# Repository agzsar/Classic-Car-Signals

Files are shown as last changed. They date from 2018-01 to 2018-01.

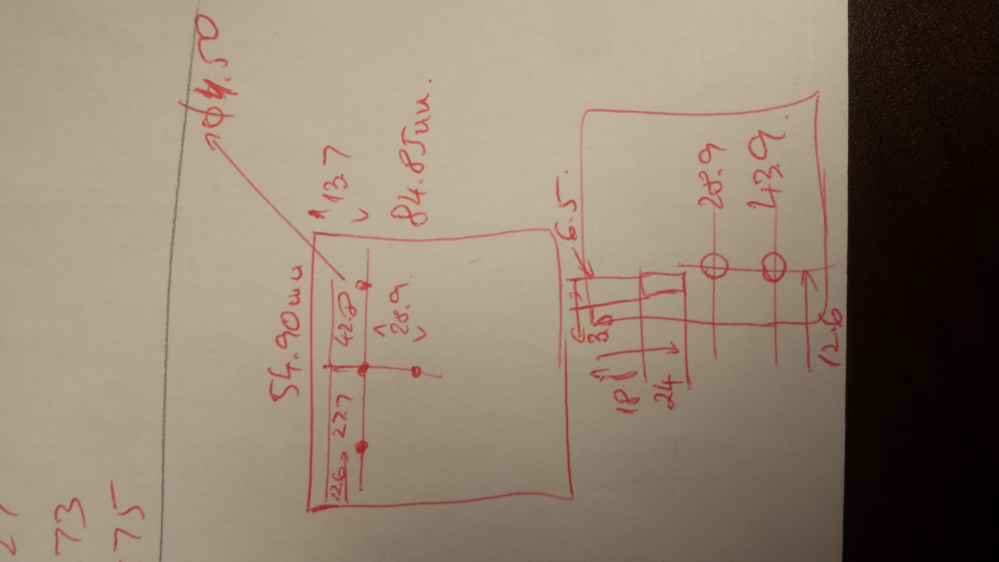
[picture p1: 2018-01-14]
9_Drawings/Remote Labels/Measurements.jpg

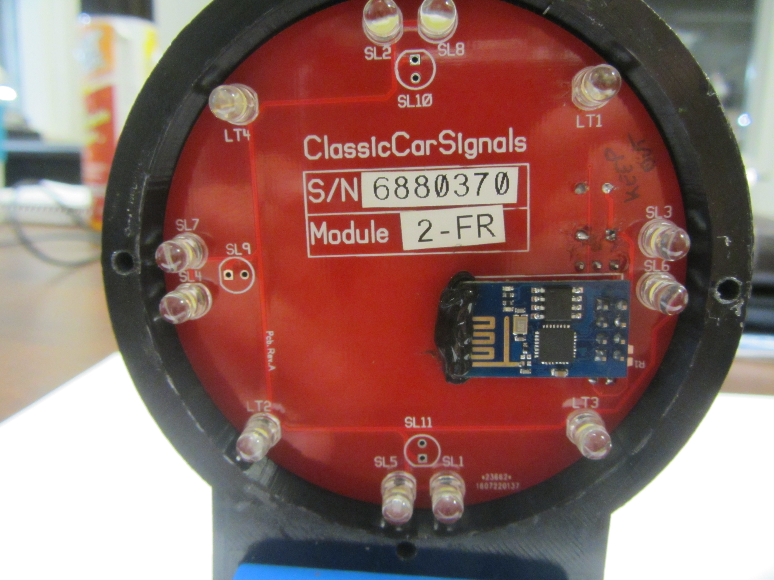
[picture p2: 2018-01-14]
97_Media/IMG_1393.JPG

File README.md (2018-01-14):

# Classic-Car-Signals
A removable turn signal system for vehicles.

General Technical Specs:
1. Five ESP8266-12F processors communicating over UDP.
2. One of the ESPs is an ACCESS POINT (REMOTE/MASTER), the other four are STATIONS (LIGHTS/SLAVES).
3. The SLAVE arduino project requires the user to configurate the "location" and "IP" of the station. Please see Read-Me file in the software folder.
4. Only one system was ever produced and tested.

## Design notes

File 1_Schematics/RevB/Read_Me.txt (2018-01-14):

1. PCBWeb was used for the PCB and schematic design.
2. See www.pcbweb.com for this free software.
3. In the slave module, R2 and R3 can be used to adjust brightness based in the specifi LED used.

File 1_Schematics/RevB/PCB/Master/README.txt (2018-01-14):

l1m          = Top layer
l2m          = Bottom layer
ss1          = Top silkscreen
ss2          = Bottom silkscreen
sm1          = Top soldermask
sm2          = Bottom soldermask
sp1          = Top solderpaste
outline      = Board outline
drill        = Plated holes Excellon file
drillnpt     = Non-Plated holes Excellon file
XYRS.csv     = Parts placement file
CCs_Master.cad = PCBWeb Project file

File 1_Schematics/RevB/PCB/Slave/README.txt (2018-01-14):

l1m          = Top layer
l2m          = Bottom layer
ss1          = Top silkscreen
ss2          = Bottom silkscreen
sm1          = Top soldermask
sm2          = Bottom soldermask
sp1          = Top solderpaste
sp2          = Bottom solderpaste
outline      = Board outline
drill        = Plated holes Excellon file
drillnpt     = Non-Plated holes Excellon file
XYRS.csv     = Parts placement file
Slave_CCs.cad = PCBWeb Project file

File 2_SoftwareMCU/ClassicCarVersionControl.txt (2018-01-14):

V1.0 Prelim
----------
- Initial Release - everything works.

V1.0
----
- Shortened pushbutton debouncing.
- Added NoReset mode on Brake Button.

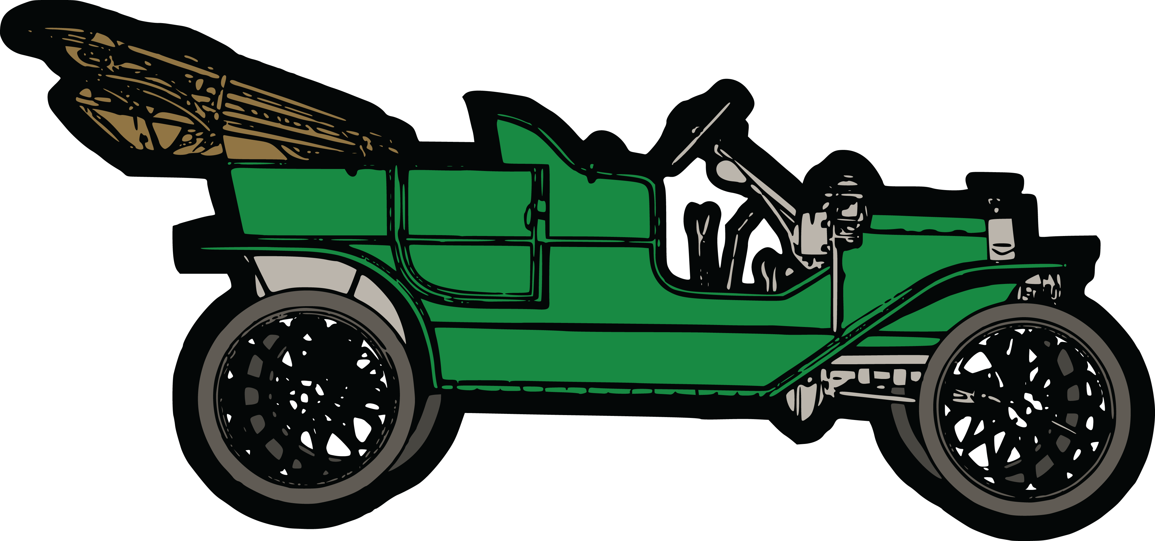
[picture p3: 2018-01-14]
9_Drawings/Remote Labels/1163-Free-Clipart-Of-A-Convertible-Green-Vintage-Car.png

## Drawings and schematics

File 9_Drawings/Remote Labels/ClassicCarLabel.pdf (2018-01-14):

### REMOTE CONTROL

### REMOTE CONTROL

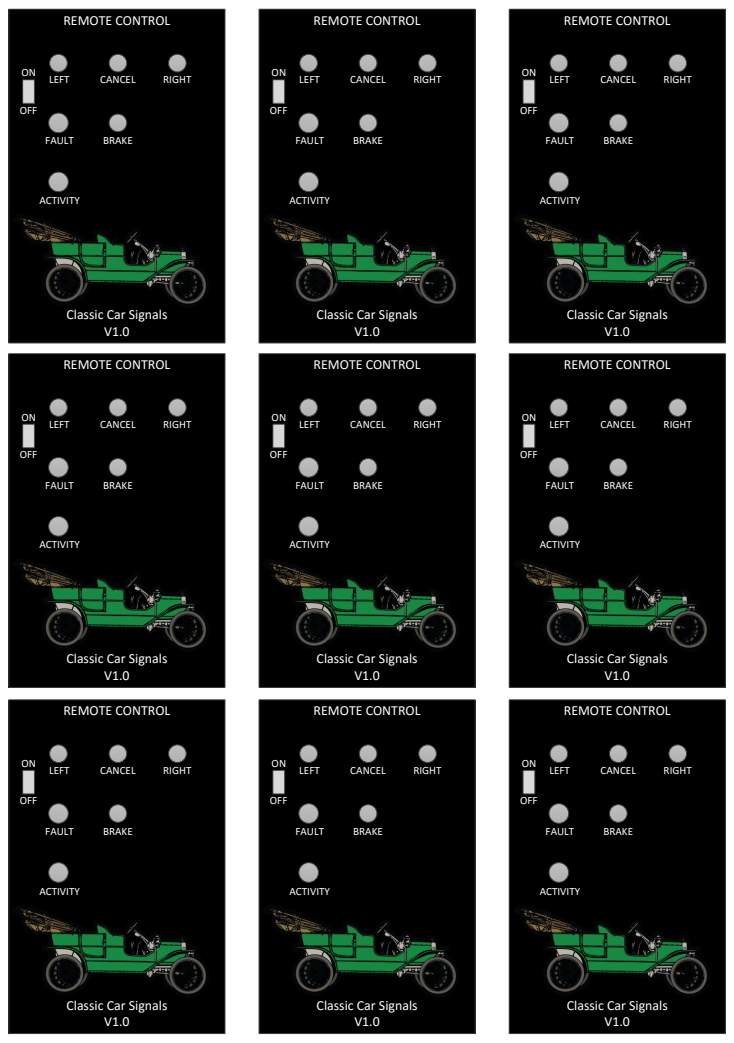
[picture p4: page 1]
OFF; FAULT; ACTIVITY; CANCEL; RIGHT; BRAKE; LEFT; REMOTE CONTROL

Classic Car Signals

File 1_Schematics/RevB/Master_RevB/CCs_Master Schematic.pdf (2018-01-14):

# 10kRESISTOR_0805

D | D

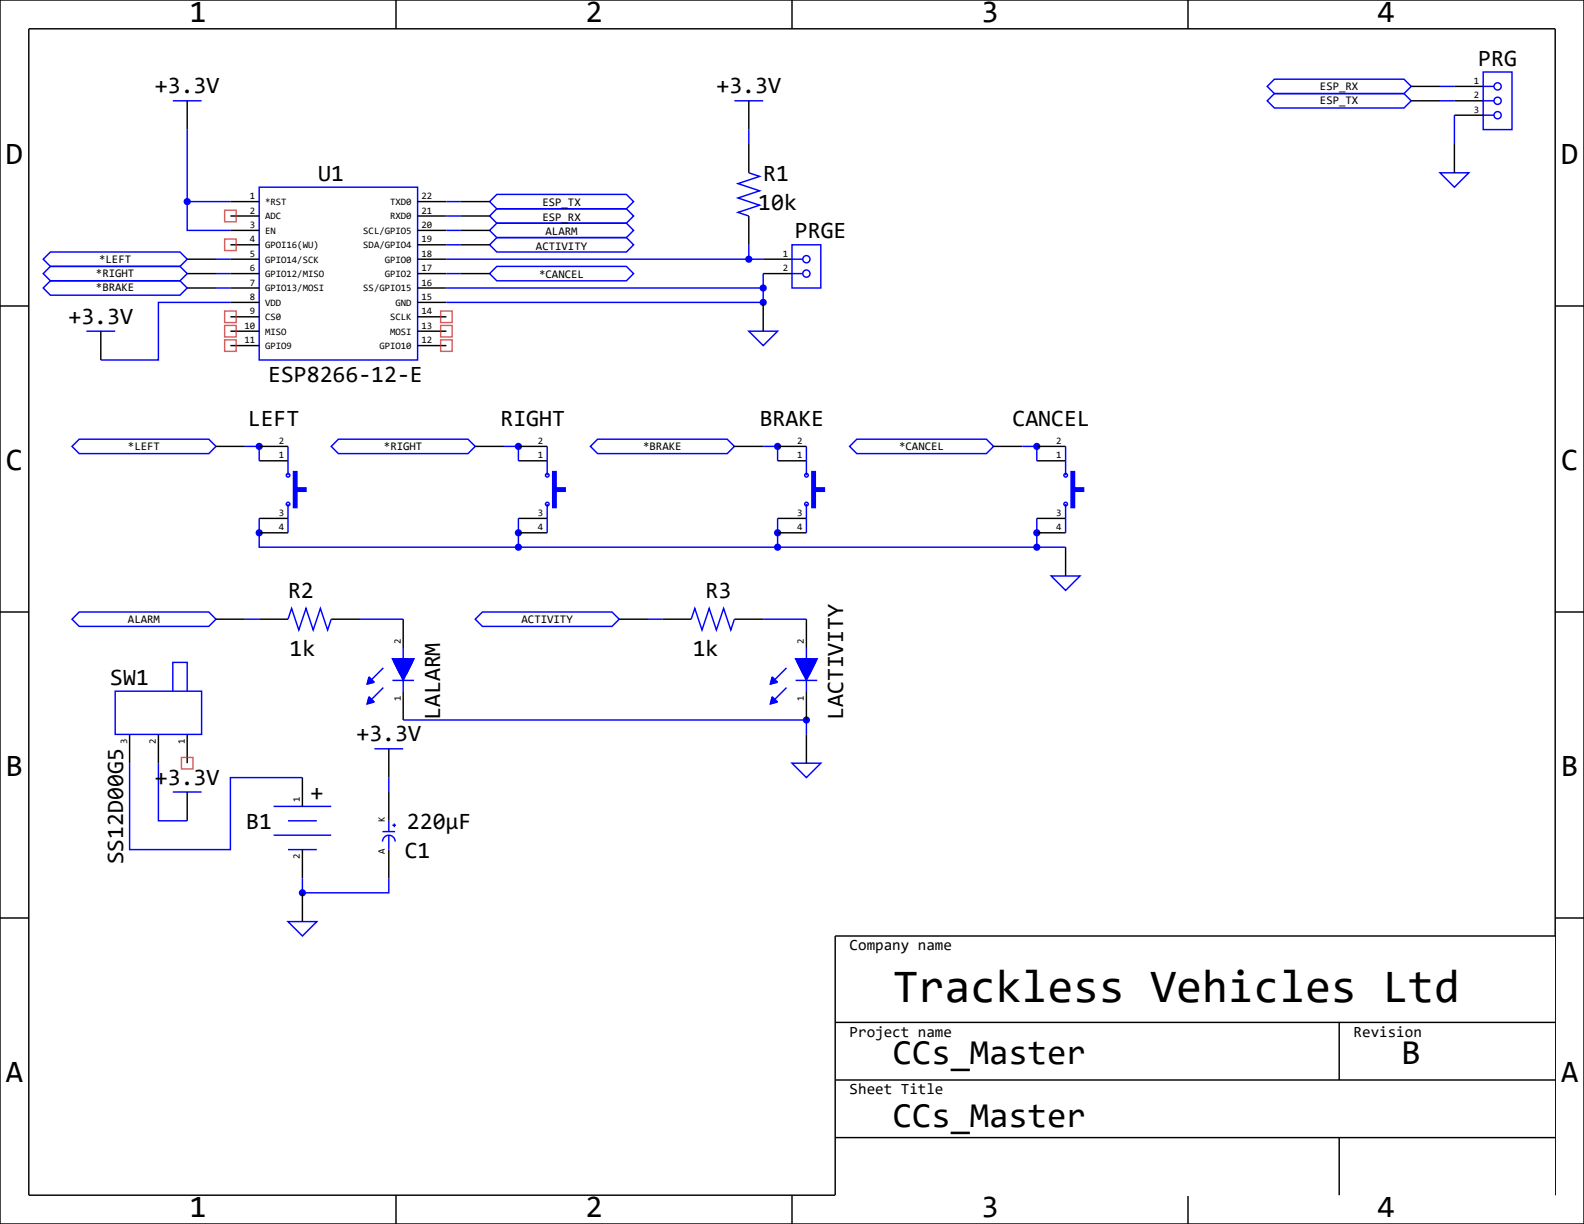
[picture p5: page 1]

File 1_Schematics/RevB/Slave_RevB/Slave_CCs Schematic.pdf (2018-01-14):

# 10kRESISTOR_0805

D | D

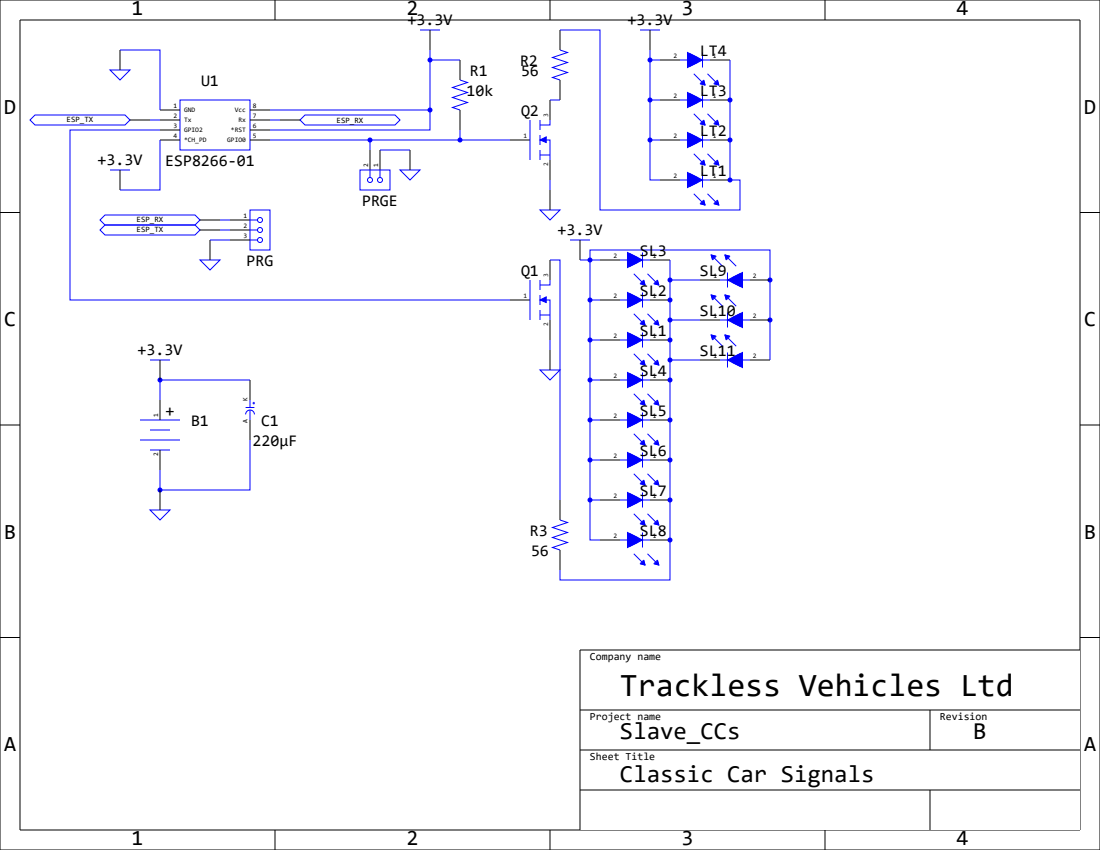
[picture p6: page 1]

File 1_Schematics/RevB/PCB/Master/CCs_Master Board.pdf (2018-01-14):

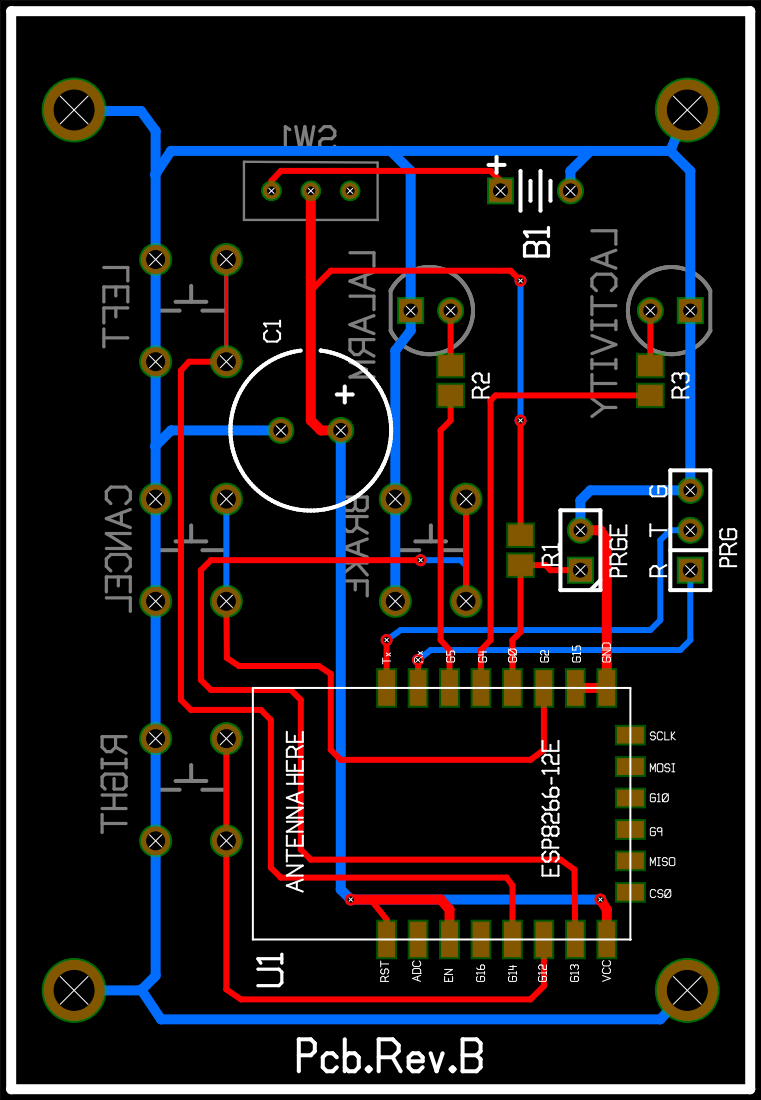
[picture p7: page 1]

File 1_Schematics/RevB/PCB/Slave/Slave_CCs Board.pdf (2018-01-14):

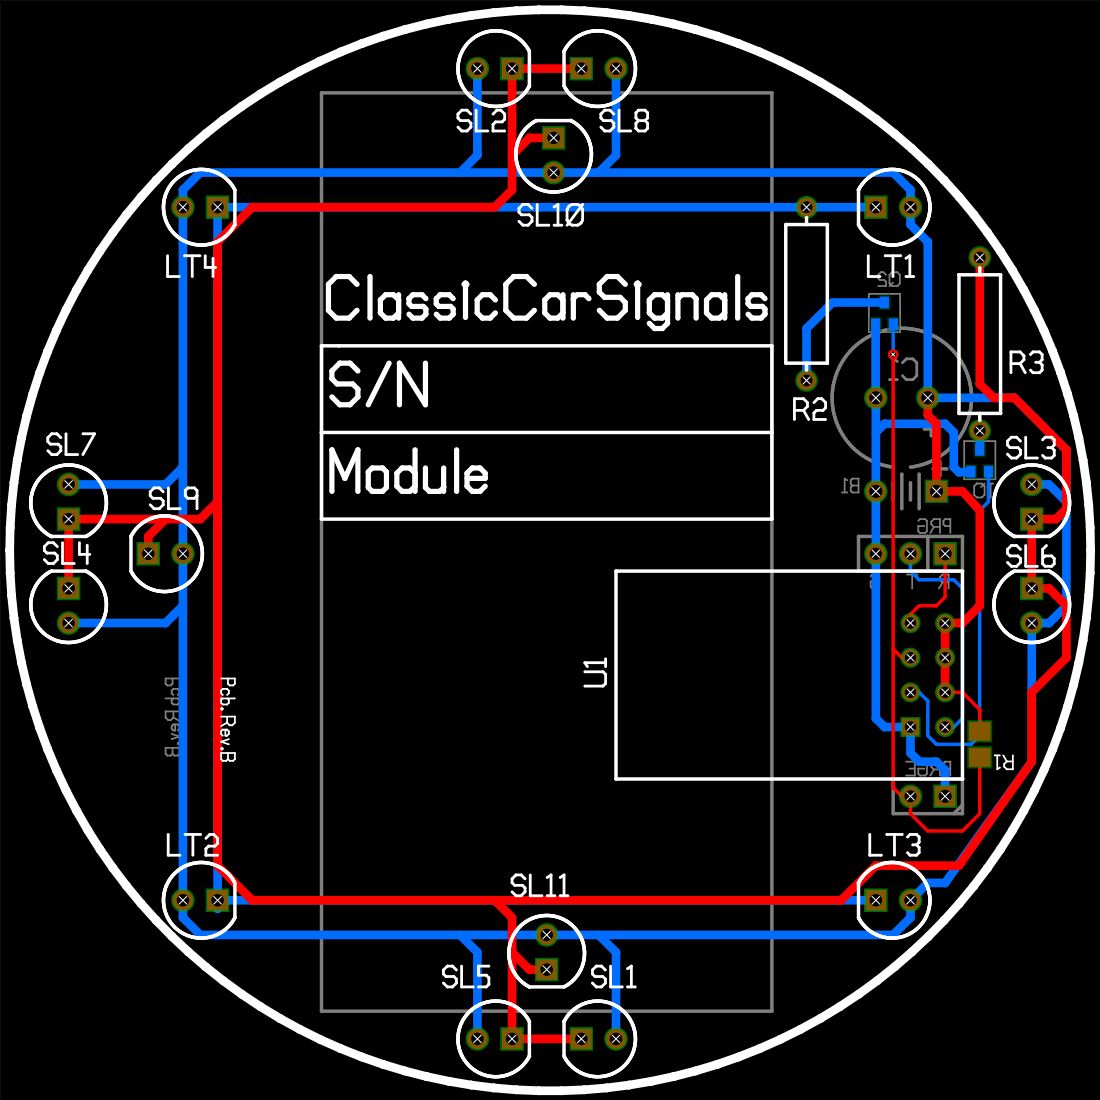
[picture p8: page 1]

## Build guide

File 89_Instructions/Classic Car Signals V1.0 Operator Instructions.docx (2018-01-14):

# Classic Car Signals

Operator Instructions

# Introduction

This project was generated from the need to equip classic cars, which at the time of manufacture lacked turn signals, with a temporary lighting system while they are operating on the road. While in many jurisdictions this is not a necessity, it will add a safety margin for the driver and passengers when travelling surrounded by other modern vehicles.

Once arrived at the destination, the temporary lighting system can be stowed away in its carrying case. This will allow the user to return the car to its original design quickly and without much effort.

# Serial Number

Each system has its own serial number. This serial number defines the matching set of lights and the remote. Lights and remotes from other serial numbers cannot be user-programmed to work un-matched.

# Identifying Modules

The lighting system has five major components: the four signal lights and the remote. They are identified as follows:

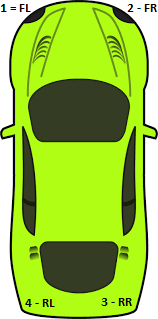
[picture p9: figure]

- Module #1 – Front Left Signal Module (FL). - Module #2 – Front Right Signal Module (FR). - Module #3 – Rear Right Signal Module (RR). - Module #4 – Rear Left Signal Module (RL). - Module #5 – Remote Control Module.

# Setting Up

1. Turn remote on.

Note: It is normal for the FAULT light to remain on while the signal modules connect to it.

2. Turn each of the signal modules on. The order does not matter.

Note: The modules will continue blinking until properly connected to the remote. Allow for up to 45 seconds.

3. Once all four signal modules have stopped blinking, the fault light should be off. System is now ready to be operated.

# Operating the system

Operating the system is done by pressing the buttons. Please refer to the below diagram.

## De-bouncing

The system is equipped with software de-bouncing of the buttons. Each button must be held down deliberately for about 250ms before the remote will engage the feature. This prevents signals from being activated too easily if the remote is dropped.

## Off State

In this state all light modules are dark and awaiting command. This is the standard mode in which the system will boot up every time.

IMPORTANT: The OFF state is the only state that allows the marker lights to be turned on or off. This is done by holding the CANCEL button for 3 seconds.

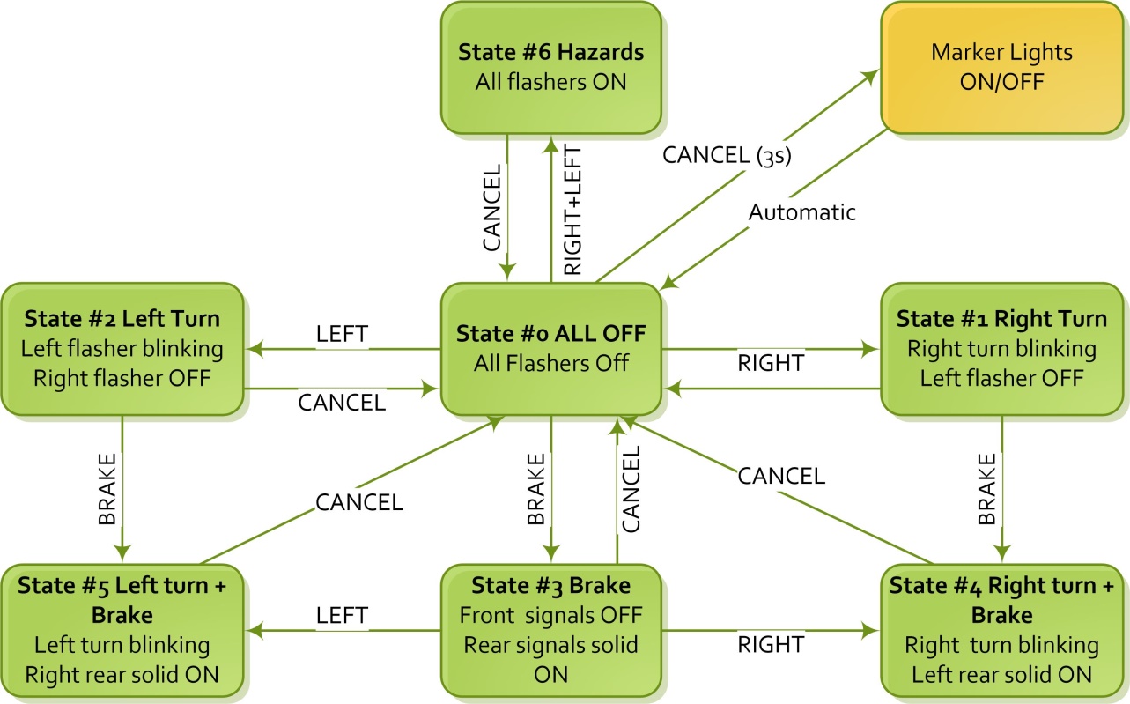
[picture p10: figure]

CANCEL

# Additional Information

While the below information is not crucial to the operation of the system, it may provide some insight during troubleshooting.

Before attempting any troubleshooting, ensure the offending module has new batteries installed. A lot of intermittent problems can occur due to depleted batteries.

## The Remote Module

The Remote module is equipped with two LEDs: FAULT and ACTIVITY. At power-up both LEDs should come on followed by both of them going off. After about five seconds the fault light will come on. This indicates that the module has booted and is looking for the signal modules. If it does not find all four modules within 15 seconds it will reboot again and commence looking for signal modules again. The system WILL NOT OPERATE without all four signal modules present.

### The ACTIVITY light operates as follows:

- If there is any active function (turn signals or brake) it will be blinking.
- If the marker lights are on it will remain lit, blinking when there is another function active.
- If no function is active, it will remain on (solid) if the marker lights are ON and will remain off if the marker lights are OFF.

### The FAULT light operates as follows:

- The fault light will be ON any time one of the signal modules cannot be reached.
- If the fault light is on for more than 15 seconds, the remote will RESET allowing all the signal modules to re-connect. This situation is highly undesirable during road travel – this is why fresh batteries are always recommended in the signal modules.

## The Signal Modules

The signal modules use the marker lights LEDs to indicate state. When the batteries are first inserted, all the LEDs will come on. After about one second the turn signal LEDs will shut off and the marker LEDs will start blinking. They will continue blinking until a connection is established to the remote. If a connection is not established within 10 seconds, the module will reboot again. This process will continue until a good connection is established. When all the lights are off the module is properly connected.

## Range

The signal modules should be within 50 meters of the remote module when the remote is inside a vehicle. In open areas, where there is no metal between the remote and the signal modules, that distance may be slightly more.

## Interference procedure

Under normal conditions, interference should not be a problem. If the system encounters interference (a signal module disconnects) the following procedure will occur automatically.

1. The disconnected module will reboot and attempt reconnection. If reconnection does not occur within 10 seconds it will reboot and try again.
2. The remote will toggle the FAULT within 2 seconds of a signal module disconnecting. If the offending module does not automatically reconnect in 15 seconds, the remote will reboot causing all the signal modules to reconnect to is as if it was just turned on.
3. Keep in mind that while connection is in progress the marker lights are blinking on the signal modules and the FAULT light will remain on.
4. Normally the situation resolves itself within 10-20 seconds.

If the above keeps occurring, it could also be a sign that one of the signal modules (or remote) is out of batteries. Replace all batteries at once for best result.

## Emergency Mode

The above mode of operation will not allow the system to function without all four Signal Modules being present and operational. This requirement can be circumvented by the following steps:

1. Ensure remote is OFF.
2. Ensure all available Signal Modules are ON.
3. Hold BRAKE button while turning the remote ON.
4. The signal modules will connect to the remote.
5. Even if not all modules are connected the remote will not issue a global reset command. It will operate with the available modules. If not all modules are connected, the FAULT light will remain on.

Using this procedure, an offending Signal Module can be identified since it will either remain OFF or keep blinking attempting to reconnect. Replace batteries in the offending module and try again by restarting the whole system. If the Signal Module remains unresponsive, it is most likely defective.

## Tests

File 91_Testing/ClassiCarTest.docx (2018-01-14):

# Classic Car Signals – Test Sheet

State / Module | 1-FL | 2-FR | 3-RR | 4-RL
0 All off | OFF | OFF | OFF | OFF
1 Right Turn | OFF | Blink | Blink | OFF
2 Left Turn | Blink | Off | Off | Blink
3 Brake | OFF | OFF | ON | ON
4 Brake + Right T | OFF | Blink | Blink | ON
5 Brake + Left T | Blink | OFF | ON | Blink
6 Hazard | Blink | Blink | Blink | Blink
10 Tail Only | Tail + OFF | Tail + OFF | Tail + OFF | Tail + OFF
11 Tail + Right | Tail + OFF | Tail + Blink | Tail + Blink | Tail + OFF
12 Tail + Left | Tail + Blink | Tail + OFF | Tail + OFF | Tail + Blink
13 Tail + Brake | Tail + OFF | Tail + OFF | Tail + ON | Tail + ON
14 Tail + Brake + RT | Tail + OFF | Tail + Blink | Tail + Blink | Tail + ON
15 Tail + Brake + LT | Tail + Blink | Tail + OFF | Tail + ON | Tail + Blink
16 Hazard + Tail | Tail + Blink | Tail + Blink | Tail + Blink | Tail + Blink

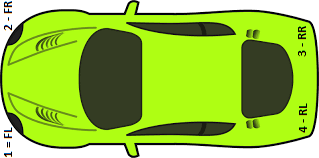
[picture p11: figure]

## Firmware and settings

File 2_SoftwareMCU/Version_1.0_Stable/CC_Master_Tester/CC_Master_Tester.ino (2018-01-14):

//VERSION INFORMATION
//-------------------
//Classic Car Signal - Master Unit
//Calin Raszga
//Version 1.0

#define debugmode
#define ALARM 5
#define ACTIVITY 4
#define CANCEL 2
#define BRAKE 13
#define RIGHT 12
#define LEFT 14

#include <ESP8266WiFi.h>
#include <WiFiUdp.h>

IPAddress ip1(192, 168, 0, 1);
IPAddress ip2(192, 168, 0, 2);
IPAddress ip3(192, 168, 0, 3);
IPAddress ip4(192, 168, 0, 4);
IPAddress ip(192, 168, 0, 5);
IPAddress gateway(192, 168, 0, 5);
IPAddress subnet(255, 255, 255, 0);

WiFiUDP Udp;

//!! CHANGE SERIAL NUMBER
const char* ssid = "6880370";
const char* password = "6880370pwd";

//SLAVE ADDRESSES
const char* LF = "192.168.0.1";
const char* RF = "192.168.0.2";
const char* RR = "192.168.0.3";
const char* LR = "192.168.0.4";

uint8_t st = 0;
uint8_t bst = 0;
uint8_t servcounter = 0;
uint8_t leftcounter = 0;
uint8_t rightcounter = 0;
uint8_t lrcounter = 0;
uint8_t cancelcounter = 0;
uint8_t cancellongcounter = 0;
uint8_t brakecounter = 0;
bool left = false;
bool right = false;
bool lr = false;
bool cancellong = false;
bool cancel = false;
bool brake = false;
bool tailon = false;
uint8_t slavecnt = 1;
unsigned int localUdpPort = 4210;
uint16_t timer1=0;
uint16_t timer2=0;
uint16_t timer3=0;
uint16_t timer4=0;
bool noreset = false;

void setup() {
  
  ESP.eraseConfig();
  WiFi.persistent(false);

  //Init super-important variables
  noreset=false;
  
  //Setup Serial Port for Diagnostic purposes
  Serial.begin(115200);
  Serial.println();
  Serial.println("CC_Master boot sequence:");
  Serial.println("Serial Communication... Done");
  
  //Setup pins
  Serial.print("Set pins to proper mode...");
  pinMode(ACTIVITY,OUTPUT);
  pinMode(ALARM,OUTPUT);
  digitalWrite(ACTIVITY,HIGH);
  digitalWrite(ALARM,HIGH);
  pinMode(LEFT,INPUT_PULLUP);
  pinMode(RIGHT,INPUT_PULLUP);
  pinMode(BRAKE,INPUT_PULLUP);
  pinMode(CANCEL,INPUT_PULLUP);
  Serial.println("Done.");
  
  //Wifi Setup and Connection
  delay(500);
  Serial.print("Setting Access Point Mode...");WiFi.mode(WIFI_AP);Serial.println("Done.");
  Serial.print("Setting Access Point IP/GT/NT...");WiFi.softAPConfig(ip, gateway, subnet);Serial.println("Done.");
  Serial.print("Starting SSID Broadcast...");WiFi.softAP(ssid, password);Serial.println("Done.");

 //Check No-Reset Condition
  noreset = !(digitalRead(BRAKE));
  Serial.print("NoResetCondition:");Serial.println(noreset);
  
  //Setting up UDP
  Serial.print("Setting UDP communication...");
  Udp.begin(localUdpPort);
  Serial.printf("Now listening at IP %s, UDP port %d\n", WiFi.localIP().toString().c_str(), localUdpPort);
  
  //Done Go to program
  Serial.println("Boot Complete. Running program.");
  digitalWrite(ACTIVITY,LOW);
  digitalWrite(ALARM,LOW);
}

void loop() {

 int packetSize = Udp.parsePacket();
 char incomingPacket[255];
 String remote;
 
 if (packetSize) {
  int len = Udp.read(incomingPacket, 255);
    if (len > 0)
    {
      incomingPacket[len] = 0;
    }
  remote=String(incomingPacket);
  if (remote==LF) {
    Serial.println("Heartbeat from:"+remote);
    timer1=0;
  }
  else if (remote==RF) {
    Serial.println("Heartbeat from:"+remote);
    timer2=0;
  }
  else if (remote==RR) {
    Serial.println("Heartbeat from:"+remote);
    timer3=0;
  }
  else if (remote==LR) {
    Serial.println("Heartbeat from:"+remote);
    timer4=0;
  }
  else {
    Serial.println("Unknown Heartbeat from:"+remote);
    timer4=0;
  } 
 }
  
  //service every half second.
  servcounter++;
  if (servcounter>=10) {
    service();
    servcounter=0;
  }

  //service buttons
  left = service_btn(&leftcounter,!digitalRead(LEFT),4);
  right = service_btn(&rightcounter,!digitalRead(RIGHT),4);
  cancel = service_btn(&cancelcounter,!digitalRead(CANCEL),4);
  cancellong = service_btn(&cancellongcounter,!digitalRead(CANCEL),40);
  brake = service_btn(&brakecounter,!digitalRead(BRAKE),4);
  lr = service_btn(&lrcounter,!digitalRead(LEFT) && !digitalRead(RIGHT),2);

  //state machine
  switch (st) {
  case 0:   //ALLOFF - Signal Case Handling
            if (lr)          {st = 6; }
            else if (left)   {st = 2; }
            else if (right)  {st = 1; }
            else if (brake)  {st = 3; }
            else             {st = st;}
    
            //Tail Light Case Handling
            if (cancellong) {
              tailon = !tailon;
            }
            break;
  case 1:   //RT - Signal Case Handling
            if (brake)         {st = 4; }
            else if (cancel)   {st = 0; }
            else               {st = st;}
            break;

  case 2:   //LT - Signal Case Handling
            if (brake)         {st = 5; }
            else if (cancel)   {st = 0; }
            else               {st = st;}
            break;

  case 3:   //BRK - Signal Case Handling
            if (cancel)        {st = 0; }
            else if (left)     {st = 5; }
            else if (right)    {st = 4; }
            else               {st = st;}
            break;

  case 4:   //RT+BRK - Signal Case Handling
  case 5:   //LT+BRK - Signal Case Handling
            if (cancel)        {st = 0; }
            else               {st = st;}
            break;

  case 6:   //HAZ - Signal Case Handling
            if (cancel)        {st = 0; }
            else               {st = st;}
            break;
            
  default:  st=0;
            break;
  }

  if (tailon) {
    bst = st+10;
  }
  else {
    bst = st;
  }

  
//  #ifdef debugmode
//    Serial.println(String(left)+String(right)+String(brake)+String(cancel)+String(lr)+String(cancellong)+" "+String(st)+" "+String(bst));
//  #endif

  service_slv(&slavecnt,bst);

  
  if (timer1<1000) {
    timer1++;
  }
  if (timer2<1000) {
    timer2++;
  }
  if (timer3<1000) {
    timer3++;
  }
  if (timer4<1000) {
    timer4++;
  }
  

  if (((timer1>300)||(timer2>300)||(timer3>300)||(timer4>300))&&!noreset) {
    Serial.println("RESET! - Slave Timeout:"+String(timer1)+" "+String(timer2)+" "+String(timer3)+" "+String(timer4));
        ESP.restart();
  }

  delay(50);
}

bool service_slv(uint8_t *counter, uint8_t state){
  uint8_t localcounter = *counter;
  uint8_t i=0;
  char reply[10];
  String replys="";
  bool result = false;

  replys ="!"+ String(bst)+"@";
  replys.toCharArray(reply,10);


  switch (localcounter) {
  case 1:
         Udp.beginPacket(ip1,localUdpPort);
         Udp.write(reply);
         Udp.endPacket();
         localcounter++;
         break;
  case 2:
         Udp.beginPacket(ip2,localUdpPort);
         Udp.write(reply);
         Udp.endPacket();
         localcounter++;
         break;
  case 3:
         Udp.beginPacket(ip3,localUdpPort);
         Udp.write(reply);
         Udp.endPacket();
         localcounter++;
         break;
  case 4:
         Udp.beginPacket(ip4,localUdpPort);
         Udp.write(reply);
         Udp.endPacket();
         localcounter=1;
         break;
  default: 
         localcounter=0;
         break;
  }
  #ifdef debugmode
    Serial.println("UDP_Packet_Out:"+String(*counter)+" "+replys);
  #endif
  *counter = localcounter;
}

bool service_btn(uint8_t *counter, int input, uint8_t limit){
  uint8_t localcounter=*counter;
  bool btn = false;
  
  if ((input)&&(localcounter<limit)) {
    localcounter++;
    btn = false;
  }
  else if ((input)&&(localcounter>=limit))
  {
    localcounter = 0;
    btn = true;
  }
  else if ((!input)&&(localcounter>0)) {
    localcounter--;
    btn = false;
  }
  *counter = localcounter;
  return btn;
}

void service() {
  //Alarm if not enough clients connected
  Serial.println("Clients:"+String(WiFi.softAPgetStationNum())+" "+String(timer1)+" "+String(timer2)+" "+String(timer3)+" "+String(timer4));
  if ((timer1>50)||(timer2>50)||(timer3>50)||(timer4>50)) {
   digitalWrite(ALARM,HIGH);    
  }
  else{
    digitalWrite(ALARM,LOW);    
  }

  //Activity flash if state is not 0 or 10.
  if (bst==0){
    digitalWrite(ACTIVITY,LOW);
  }
  else if (bst==10) {
    digitalWrite(ACTIVITY,HIGH);
  }
  else {
    digitalWrite(ACTIVITY,!digitalRead(ACTIVITY));    
  }
}

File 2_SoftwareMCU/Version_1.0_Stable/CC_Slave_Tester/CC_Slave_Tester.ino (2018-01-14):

//VERSION INFORMATION
//-------------------
//Classic Car Signal - Slave Unit
//Version 1.0

//!!CHANGE LOCATION
#define location 1 //(1=FL 2=FR 3=RR 4=RL)
#define testmode 0
#define debugmode
#define TL 0
#define SL 2

#include <ESP8266WiFi.h>
#include <WiFiUdp.h>

//Global Variables 
//!!CHANGE IP
IPAddress ip(192, 168, 0, 1); //(1=FL 2=FR 3=RR 4=RL)
IPAddress gateway(192, 168, 0, 5);
IPAddress subnet(255, 255, 255, 0);

WiFiUDP Udp;

//!!!CHANGE SERIAL NUMBER
const char* ssid = "6880370";
const char* password = "6880370pwd";

uint8_t blink1;
uint8_t blink2;
uint8_t blink3;
uint8_t on1;
uint8_t on2;
uint8_t on3;
uint8_t st;
uint8_t blcnt=0;
uint8_t hrt=0;
unsigned int localUdpPort = 4210;
String replys = ip.toString();
char reply[16];


void setup() {
  uint8_t concnt=0;

  //Initialize vars as needed
  st=0;
  
  //Start Fresh Configuration
  ESP.eraseConfig();
  WiFi.persistent(false);
  
  //Setup Serial Port for Diagnostic purposes
  Serial.begin(115200);
  Serial.println();
  Serial.println("CC_Slave boot sequence:");
  Serial.println("Serial Communication... Done");
  
  //Setup pins
  Serial.print("Set pins to output mode...");
  pinMode(TL,OUTPUT);
  pinMode(SL,OUTPUT);
  digitalWrite(TL,HIGH);
  
  Serial.println("Done.");

  //Wifi Setup and Connection
  delay(500);
  Serial.print("Setting Station Mode...");WiFi.mode(WIFI_STA);Serial.println("Done.");
  Serial.print("Setting IP/GT/NM...");  WiFi.config(ip, gateway, subnet);Serial.println("Done.");
  Serial.print("Connecting_");WiFi.begin(ssid, password);
  concnt=0;
  while (WiFi.status() != WL_CONNECTED) {
    if(concnt > 20){
       Serial.print("- can't connect, restarting");    
       ESP.restart();
    }
    delay(500);
    Serial.print(".");
    concnt++;
    digitalWrite(TL,!digitalRead(TL));
  }
  digitalWrite(TL,LOW);
  Serial.print(WiFi.localIP());Serial.println("-Done.");

  //Setting up UDP
  Serial.print("Setting UDP communication...");
  Udp.begin(localUdpPort);
  Serial.printf("Now listening at IP %s, UDP port %d\n", WiFi.localIP().toString().c_str(), localUdpPort);
  
  //Setup Location Specific
  Serial.print("Determining Location...");Serial.print(location);Serial.println(" ...Done");
  switch (location) {
  case 1: //Left Front
    on1=9;
    on2=9;
    on3=9;
    blink1=6;
    blink2=5;
    blink3=2;
    break;
  case 2: //Right Front
    on1=9;
    on2=9;
    on3=9;
    blink1=6;
    blink2=4;
    blink3=1;
    break;
  case 3: //Right Rear
    on1=5;
    on2=3;
    on3=9;
    blink1=6;
    blink2=4;
    blink3=1;
    break;
  case 4: //Left Rear
    on1=4;
    on2=3;
    on3=9;
    blink1=6;
    blink2=5;
    blink3=2;
    break;
  default:
    on1=9;
    on2=9;
    on3=9;
    blink1=9;
    blink2=9;
    blink3=9;
    break;
  }
  Serial.println(" ...Done");

  //Done Go to program
  Serial.println("Boot Complete. Running program.");
}

void loop() {
  uint8_t st_bl;
  char incomingPacket[255];
  String incomingString;
  String stateString;
  
  int packetSize = Udp.parsePacket();

  if (packetSize) {
    int len = Udp.read(incomingPacket, 255);
    if (len > 0)
    {
      incomingPacket[len] = 0;
    }
    incomingString=String(incomingPacket);
    Serial.printf("Received %d bytes from %s, port %d, ", packetSize, Udp.remoteIP().toString().c_str(), Udp.remotePort());
    Serial.println("UDP packet contents:"+incomingString);
    if (incomingString[0]=='!') {
      hrt=0;    
      stateString = incomingString.substring(1,incomingString.indexOf("@"));
      st=stateString.toInt();
      Serial.print("NewState:"+String(st)+" Ack:");

      replys.toCharArray(reply,16);
      Serial.println(reply);
      Udp.beginPacket(gateway,localUdpPort);
      Udp.write(reply);
      Udp.endPacket();
    }
  }

  if (st>9) { 
    digitalWrite(TL,HIGH);
    st_bl=st-10;
  } 
  else {
    digitalWrite(TL,LOW);
    st_bl=st;
  }
  
  if ((st_bl==blink1)||(st_bl==blink2)||(st_bl==blink3)){
    blcnt++;
    if (blcnt>10) {
      digitalWrite(SL,!digitalRead(SL));
      blcnt=0;
    }
  }
  else if ((st_bl==on1)||(st_bl==on2)||(st_bl==on3)){
    digitalWrite(SL,HIGH);
    blcnt=0;
  }
  else {
    blcnt=0;
    digitalWrite(SL,LOW);
  }

  hrt++;
  
  if (hrt>40) {
    Serial.println("STATE Request Timeout - Restarting!");    
       ESP.restart();
  }

  delay(50);  

}
